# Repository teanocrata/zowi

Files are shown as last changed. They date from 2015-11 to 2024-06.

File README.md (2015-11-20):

# zowi

##License



All these products are released under [Creative Commons Attribution-ShareAlike 4.0 International License](http://creativecommons.org/licenses/by-sa/4.0/).

Todos estos productos están liberados mediante [Creative Commons Attribution-ShareAlike 4.0 International License](http://creativecommons.org/licenses/by-sa/4.0/).

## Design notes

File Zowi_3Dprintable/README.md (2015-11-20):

<table>
<tr>
<td>
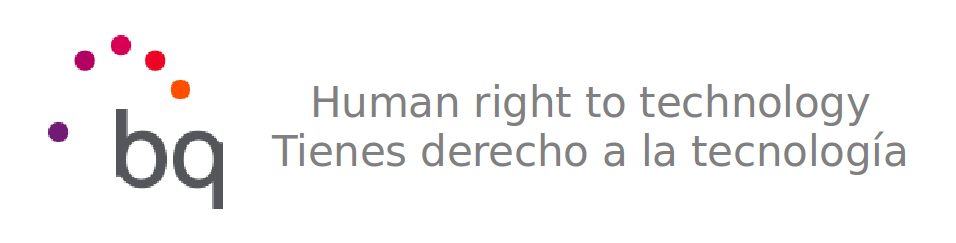
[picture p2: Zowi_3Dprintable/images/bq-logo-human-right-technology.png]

</td>
</tr>
</table>

# ZOWI

In this repository you will find the source files for the **bq Zowi** robot. If you are missing something, please do not hesitate to [file an issue on github](https://github.com/bq/zowiissues)

En este repositorio se encuentran los ficheros fuente del robot **Zowi de bq**. Si echas en falta algo, no dudes en [rellenar una tarea en github](https://github.com/bq/zowi/issues)

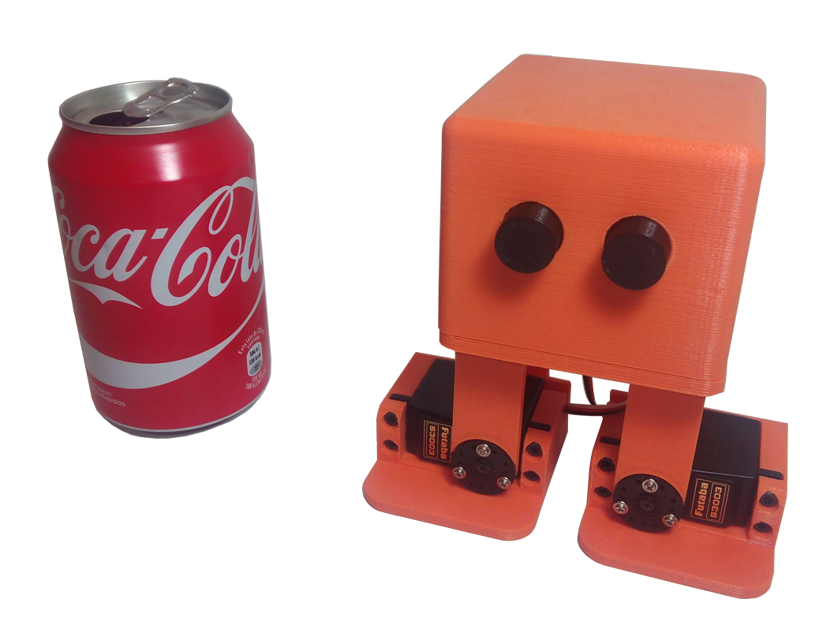
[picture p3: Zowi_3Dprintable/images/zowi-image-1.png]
 

More information in this post in DIWO: [Zowi, introducción a los robots bípedos](http://diwo.bq.com/zowi-introduccion-a-los-robots-bipedos/) (In spanish)

## Designed in Freecad

Zowi is not only an open source robot, but it has also been designed using the open source tool FreeCAD. This way, anyone can open the parts, study them, modify them and distribute the modifications

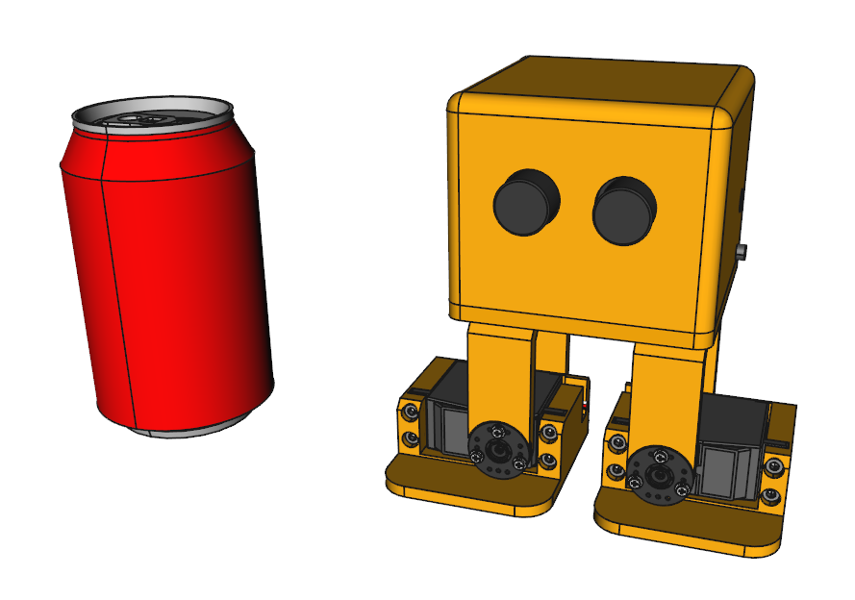
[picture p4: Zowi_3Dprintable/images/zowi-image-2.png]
 

# BOM: Bill of Materials

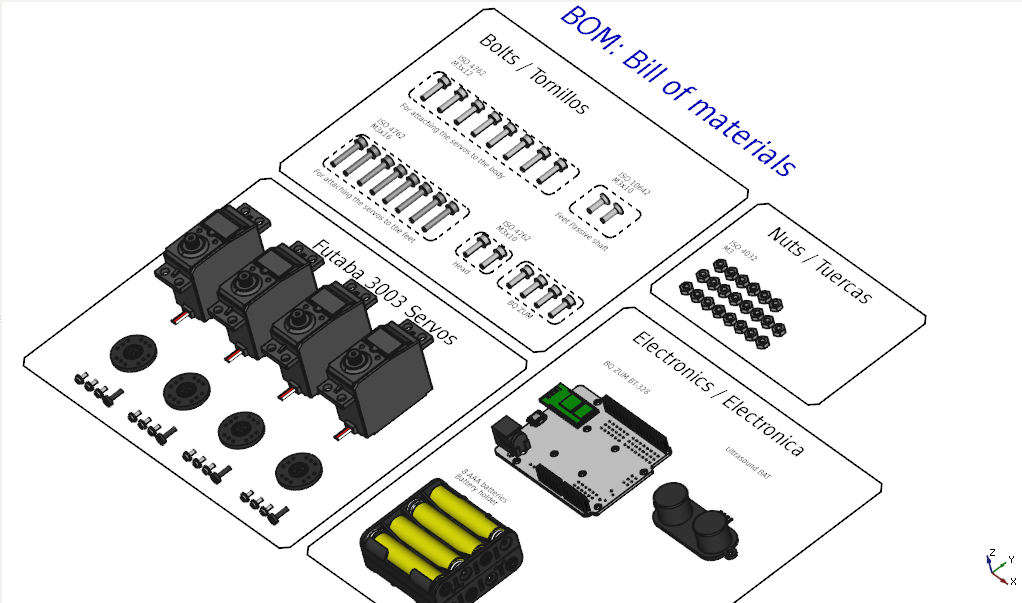
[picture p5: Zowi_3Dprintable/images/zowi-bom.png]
 

* 4 Futaba 3003 servos or compatibles
* 6 M3x10 Bolts (ISO 4762)
* 2 M3x10 Bolts (ISO 10642)
* 8 M3x12 Bolts (ISO 4762)
* 8 M3x16 Bolts (ISO 4762)
* 22 M3 nuts (ISO 4032)
* 1 BQ ZUM BT328 or Arduino
* 4 x 2 AAA Battery holder
* 8 AAA bateries

# License 



This robot is licensed under a [Creative Commons Attribution-ShareAlike 4.0 International License](http://creativecommons.org/licenses/by-sa/4.0/). Please read the LICENSE files for more details.

Este robot tiene una licencia [Creative Commons Attribution-ShareAlike 4.0 International License](http://creativecommons.org/licenses/by-sa/4.0/). Por favor, lea los ficheros LICENSE para más detalles

Original concept by [k120189](http://www.thingiverse.com/k120189/about) on [Thingiverse](http://www.thingiverse.com/thing:43708)

More information: [Zowi CC-BY-SA](http://diwo.bq.com/zowi-cc-by-sa/)

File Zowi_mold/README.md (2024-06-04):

<table>
<tr>
<td>

</td>
</tr>
</table>

# ZOWI

In this repository you will find the source files for the **Zowi** robot. If you are missing something, please do not hesitate to [file an issue on github](https://github.com/bq/zowiissues)

En este repositorio se encuentran los ficheros fuente del robot **Zowi**. Si echas en falta algo, no dudes en [rellenar una tarea en github](https://github.com/bq/zowi/issues)

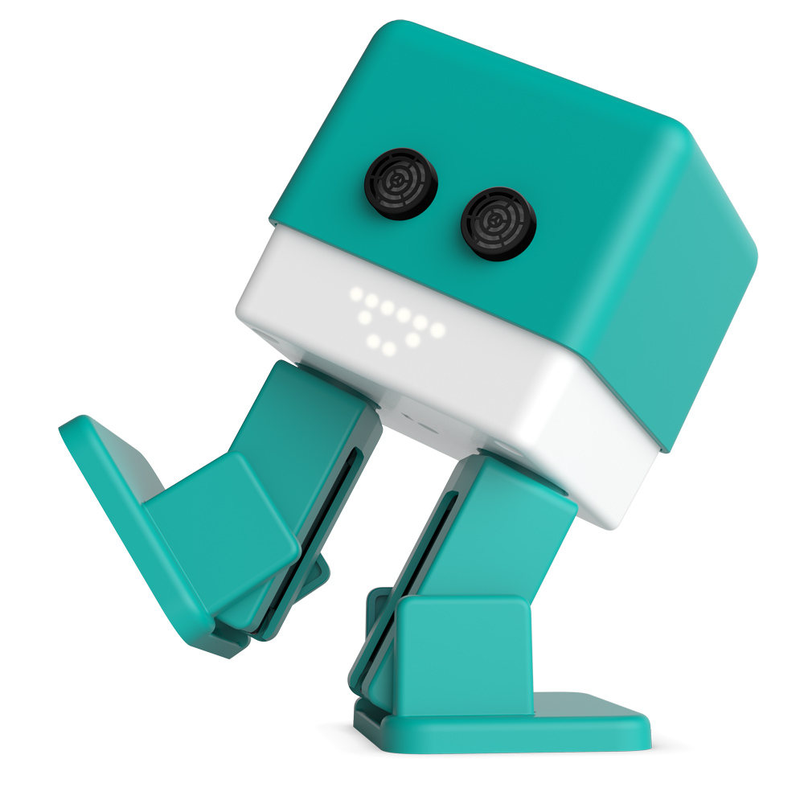
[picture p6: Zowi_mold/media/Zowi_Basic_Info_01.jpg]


More information in the official website: [Zowi](http://zowi.bq.com/)

# License



This robot is licensed under a [Creative Commons Attribution-ShareAlike 4.0 International License](http://creativecommons.org/licenses/by-sa/4.0/). Please read the LICENSE files for more details.

Este robot tiene una licencia [Creative Commons Attribution-ShareAlike 4.0 International License](http://creativecommons.org/licenses/by-sa/4.0/). Por favor, lea los ficheros LICENSE para más detalles

Derived from [Zowi by bqlabs](https://github.com/bqlabs/zowi)

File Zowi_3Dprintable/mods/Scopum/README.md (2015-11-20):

# Scopum

Scopum has been created by [HackLab UPM Bq](http://hacklabupm.bq.com/doku.php?id=start). 
He has been designed in order to have a battle with more Scopums. He has a target in the chest with a receptor fototransistor and a emisor diode in the weapon which is in his arm. Besides, he include a buzzer destinated to make sound when he shoots and when he dies.

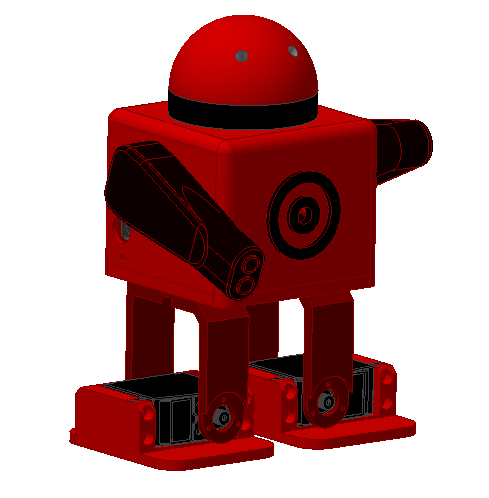
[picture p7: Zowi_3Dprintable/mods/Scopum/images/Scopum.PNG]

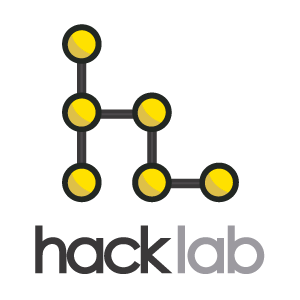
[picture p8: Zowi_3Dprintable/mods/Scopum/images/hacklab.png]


Original concept by [JavierIH](https://github.com/JavierIH) on [Github](https://github.com/bq/zowi)

# License 



This robot is licensed under a [Creative Commons Attribution-ShareAlike 4.0 International License](http://creativecommons.org/licenses/by-sa/4.0/). Please read the LICENSE files for more details.

Este robot tiene la licencia [Creative Commons Attribution-ShareAlike 4.0 International License](http://creativecommons.org/licenses/by-sa/4.0/). Por favor, lea los ficheros LICENSE para más detalles

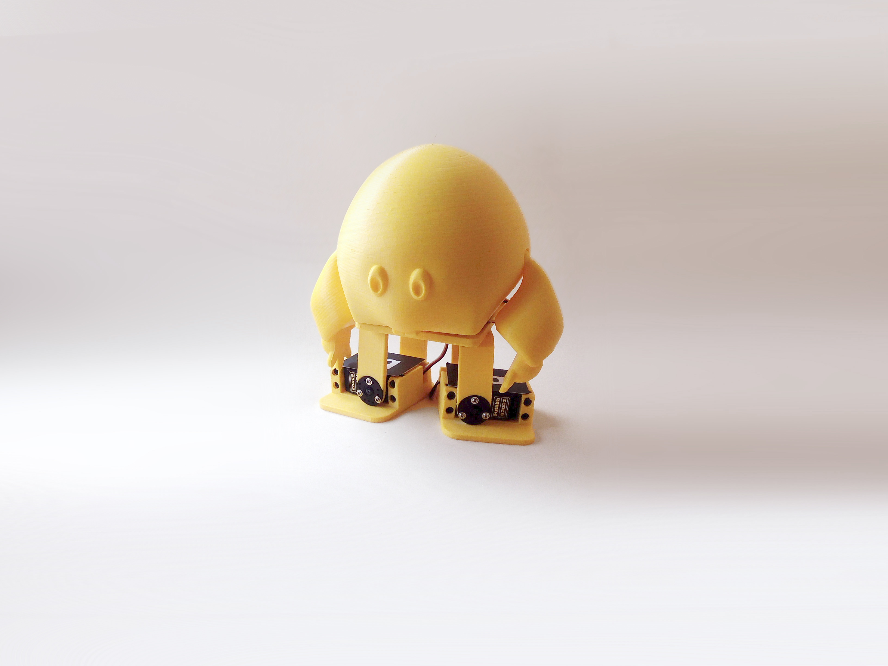
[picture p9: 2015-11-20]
Zowi_3Dprintable/mods/JIM/images/JIM_2.jpg

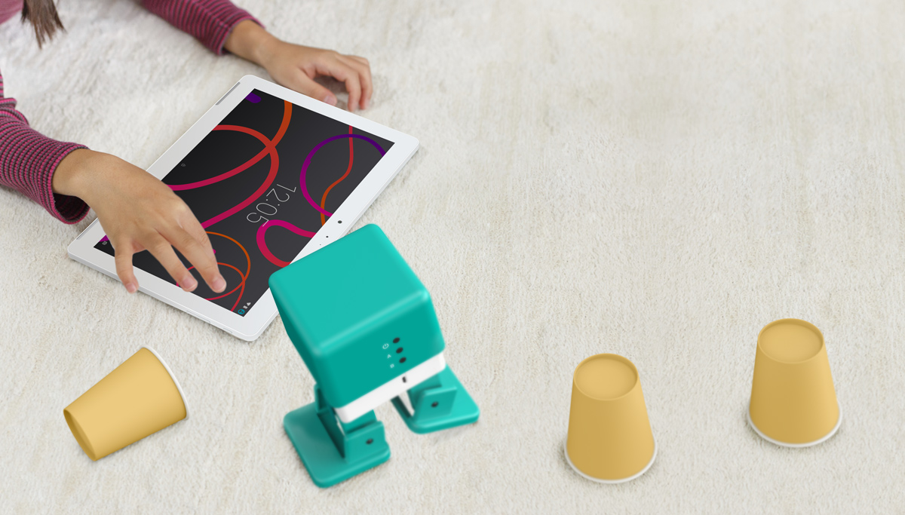
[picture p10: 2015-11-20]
Zowi_mold/media/Zowi_Integracion_app_dise2.jpg

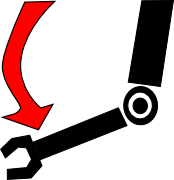
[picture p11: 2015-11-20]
Zowi_3Dprintable/mods/Scopum/code/Protocoder/images/izquierdo_abajo.png

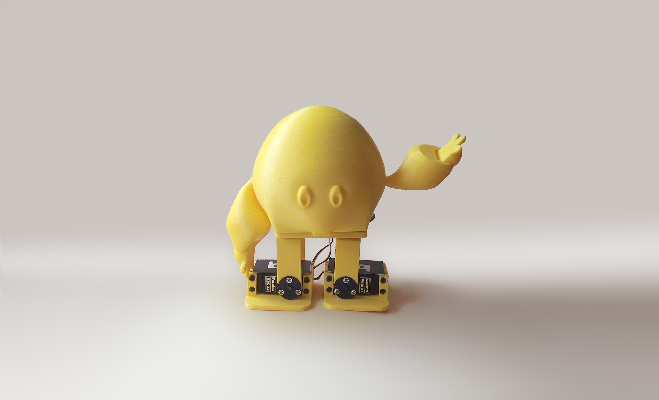
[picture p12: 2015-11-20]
Zowi_3Dprintable/mods/JIM/images/JIM_1.jpg

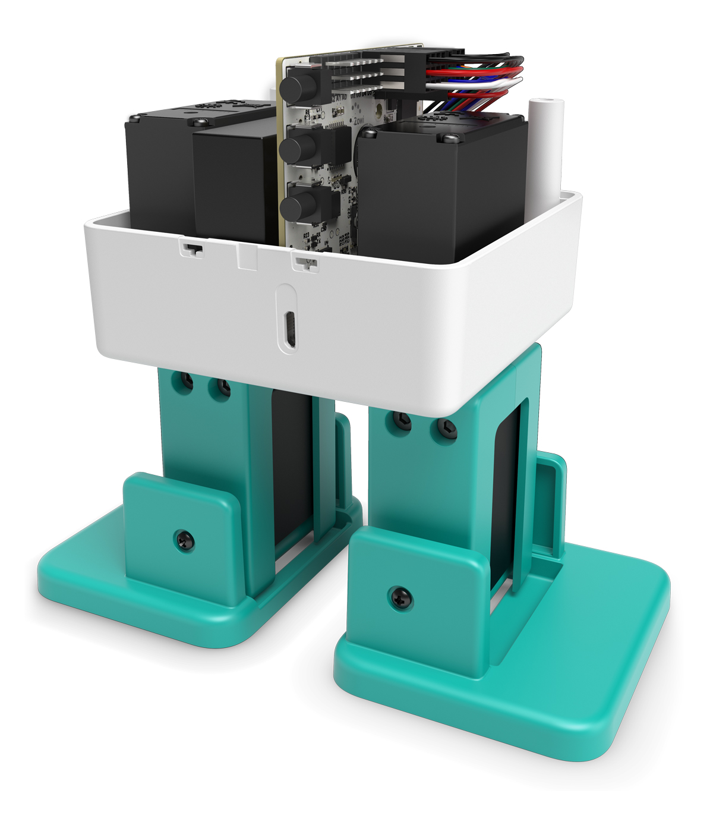
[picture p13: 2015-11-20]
Zowi_mold/media/Zowi_lookbook_interior_01.jpg

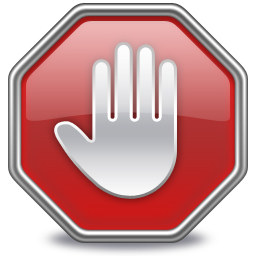
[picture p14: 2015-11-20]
Zowi_3Dprintable/code/protocoder/images/stop.png

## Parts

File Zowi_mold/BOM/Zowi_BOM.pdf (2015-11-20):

Name | Quantity | Made in
Electronics | Main Board | 1 | Valencia (Spain)
| LED Matrix | 1 | Valencia (Spain)
| Ultrasonic Board | 1 | Valencia (Spain)
| Battery 4040mAh | 1 | Valencia (Spain)
| Futaba S3003 servo | 4 | Taiwan
| Ultrasonic cable | 1 | China
| LED Matrix cable | 1 | China
| MJ622 black round button | 3 | France
| Light filter | 1 | Madrid (Spain)
Plastic parts | Zowi Top housing | 1 | Poland
| Zowi Base | 1 | Poland
| Zowi Leg back | 2 | Poland
| Zowi Leg front | 2 | Poland
| Zowi Foot left | 1 | Poland
| Zowi Foot right | 1 | Poland
| Zowi Foot cover | 2 | Poland
Screws | Socket head cap screws M3x10 (DIN912) Black | 20 | Navarra (spain)
| Celoplast screws for plastic CL 81 Z - Ø2.3 x 6mm Zin | 2 | Spain/China
| Celoplast screws for plastic CL 81 Z - Ø2.0 x 8mm Zin | 6 | Spain/China
| TH030H055 inserts for M3 screws | 20 | France

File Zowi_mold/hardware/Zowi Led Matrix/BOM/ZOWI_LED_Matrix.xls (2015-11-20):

 |  |  |  |  | BILL OF MATERIALS
TITLE: | BOM-Complete For Project [ZOWI_LED_Matrix.PrjPcb] (No PCB Document Selected) |  | REV | DATE | AUTHOR |  | DATE | AUTHOR
VARIANT: |  |  | 00 | 16/11/2015 | Jon Goitia | MADE BY: | 16/11/2015 | Jon Goitia
DOCUMENT: | Bill of Materials |  | 01 |  |  | VERIFIED BY:
PROJECT: | ZOWI_LED_Matrix.PrjPcb |  | 02 |  |  | APPROVED BY:
NOTE | ITEM | Designator | Description |  |  | OrderingCode | Manufacturer | Footprint | Quantity | Value
 | 1 | C1, C6 | Capacitor SMD |  |  | C0603C225K4PAC | Kemet | C0603 | 2 | 2.2uF ±10% 16V
 | 2 | C2, C3, C4, C5 | Capacitor SMD |  |  | C0402C104K4RAC | Kemet | C0402 | 4 | 100nF ±10% 16V
 | 3 | D1, D2, D3, D4 | Protection, Transient Suppression Diode |  |  | ESD9L5.0ST5G | ON Semiconductor | SOD923 | 4
 | 4 | J1 | Connector, 1x5 MTE Angled Header 2.54mm |  |  | 5-103635-4 | TE Connectivity | 1x5 MTE Angled Header 2.54mm | 1 | 5
 | 5 | LD1A, LD1B, LD1C, LD1D, LD1E, LD1F, LD2A, LD2B, LD2C, LD2D, LD2E, LD2F, LD3A, LD3B, LD3C, LD3D, LD3E, LD3F, LD4A, LD4B, LD4C, LD4D, LD4E, LD4F, LD5A, LD5B, LD5C, LD5D, LD5E, LD5F | LED |  |  | LTW-170ZDC | Lite-On | LED0805 | 30 | White
 | 6 | R1, R2, R3, R4, R5, R6, R7, R8 | Resistor |  |  | CAY16-271J4LF | Bourns | 4xArray_1206 | 8 | 270R ±0,5% 0,0625W
 | 7 | U1, U2, U3, U4 | Shift Register 8BIT |  |  | 74HC595BQ | NXP | DHVQFN16-2.5x3.5MM | 4
NOTES:

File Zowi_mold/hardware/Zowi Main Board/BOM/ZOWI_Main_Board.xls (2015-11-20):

 |  |  |  |  | BILL OF MATERIALS
TITLE: | BOM_Complete For Project [ZOWI_Main_Board.PrjPCB] (No PCB Document Selected) |  | REV | DATE | AUTHOR |  | DATE | AUTHOR
VARIANT: |  |  | 00 | 26/10/2015 | Raúl de Pablos | MADE BY: | 26/10/2015 | Raúl de Pablos
DOCUMENT: | Bill of Materials |  | 01 |  |  | VERIFIED BY:
PROJECT: | ZOWI_Main_Board.PrjPCB |  | 02 |  |  | APPROVED BY:
NOTE | ITEM | Designator | Description |  |  | OrderingCode | Manufacturer | Footprint | Quantity | OrderingCode 2 | Manufacturer 2 | Value
 | 1 | BUZZ2 | Buzzer |  |  | KXG1205 | Kingstate Elect. | BUZZER_12 | 1
 | 2 | C1, C2, C8, C11, C12, C13, C14, C17, C23, C26, C27, C30, C31, C33, C36, C50, C52 | Capacitor SMD |  |  | C0402C104K4RAC | Kemet | C0402 | 17 |  |  | 100nF ±10% 16V
 | 3 | C3, C4, C5, C24, C25, C28, C35, C49 | Capacitor SMD |  |  | C0603C105K4PAC | Kemet | C0603 | 8 |  |  | 1uF ±10% 16V
 | 4 | C9 | Capacitor SMD |  |  | GJM1555C1H120JB01D | Murata | C0402 | 1 |  |  | 12pF ±5% 50V
 | 5 | C10 | Capacitor SMD |  |  | C1608X5R1C475K080AC | TDK | C0603 | 1 |  |  | 4.7uF ±10% 16V
 | 6 | C15, C40, C45 | Capacitor SMD |  |  | C0603C225K4PAC | Kemet | C0603 | 3 |  |  | 2.2uF ±10% 16V
 | 7 | C16, C18, C19, C20, C21 | Capacitor SMD |  |  | GRM219R61C226ME15K | Murata | C0805 | 5 |  |  | 22uF ±20% 16V
 | 8 | C22 | Capacitor, Electrolytic, SMD |  |  | EEE-0JA221WP | Panasonic | CASE_D | 1 |  |  | 220uF 6V3
 | 9 | C32, C39, C44, C47, C51 | Capacitor SMD |  |  | C0402C103K4RAC | Kemet | C0402 | 5 |  |  | 10nF ±10% 16V
 | 10 | C34 | Capacitor SMD |  |  | C2012X7R2E472K085AM | TDK | C0805 | 1 |  |  | 4700pF ±10% 250V
 | 11 | C37, C38 | Capacitor SMD |  |  | C0402C470K4GAC | Kemet | C0402 | 2 |  |  | 47pF ±10% 16V
 | 12 | C41, C42 | Capacitor SMD |  |  | C0402C100K4GAC | Kemet | C0402 | 2 |  |  | 10pF ±10% 16V
 | 13 | C43 | Capacitor SMD |  |  | GRM1555C1H180JA01D | Murata | C0402 | 1 |  |  | 18pF ±5% 50V
 | 14 | C46 | Capacitor SMD |  |  | C0402C150K4GAC | Kemet | C0402 | 1 |  |  | 15pF ±10% 16V
 | 15 | C48 | Capacitor SMD |  |  | C0402C473K4RAC | Kemet | C0402 | 1 |  |  | 47nF ±10% 16V
 | 16 | Cs1 | Capacitor SMD |  |  | GJM1555C1H3R7WB01D | Murata | C0402 | 1 |  |  | 3,7pF ±7% 50V
 | 17 | D1, D4 | Dual Schottky Diode |  |  | BAT54S | NXP | SOT23-3 | 2 | BAT54S | Vishay | 200mA 30V
 | 18 | D2, D3 | Schottky Diode |  |  | PMEG3030EP | NXP | SOD128 | 2 |  |  | 3A 30V
 | 19 | F1 | Protection, PTC Resettable Fuse |  |  | MF-MSMF150/24X | Bourns | F1812 | 1
 | 20 | F2 | Protection, USB ESD |  |  | 82400152 | Würth | SOT563 | 1 | CDSOT563-0502 | Bourns
 | 21 | F3 | Filter, Band Pass, Balun |  |  | 2450FB15K0005E | Johanson Technlogy | 2450FB15K0005 | 1 | DBF81F104-CSR-T | Soshin
 | 22 | J1 | Connector, 1x6 pin Header 2.54mm |  |  | TSW-106-07-T-S-BLUE | Samtec | 1x6 Pin Header 2.54 | 1
 | 23 | J2 | Connector, 1x6 pin Header 2.54mm |  |  | TSW-106-07-T-S-RED | Samtec | 1x6 Pin Header 2.54 | 1
 | 24 | J3 | Connector, 1x6 pin Header 2.54mm |  |  | TSW-106-07-T-S | Samtec | 1x6 Pin Header 2.54 | 1 | 613 006 111 21 | Würth Elektronik | 6
 | 25 | J4 | Connector, 6 pin Dual Header 2.54mm |  |  | TSW-103-07-T-D | Samtec | 2x3 Pin Header 2.54 | 1 | 613 006 211 21 | Würth Elektronik | 6
 | 26 | J5, J8 | Connector, 1x4 pin Header 2.54mm |  |  | TSW-104-07-T-S | Samtec | 1x4 Pin Header 2.54 | 2 | 613 004 111 21 | Würth Elektronik | 4
 | 27 | J6 | Connector, 1x4 pin Header 2.54mm |  |  | TSW-104-07-T-S-NATURAL | Samtec | 1x4 Pin Header 2.54 | 1
 | 28 | J7 | Connector, 1x4 pin Header 2.54mm |  |  | TSW-104-07-T-S-RED | Samtec | 1x4 Pin Header 2.54 | 1
 | 29 | J9 | 1x3 PH connector |  |  | S3B-PH-SM4-TB | JST | S3B-PH-SM4-TB | 1
 | 30 | J10 | Connector, USB Micro B |  |  | 10118194-0001LF | FCI | USB_B_W_REAR_PEGS | 1
 | 31 | L1 | Inductor, Power, SMD |  |  | SRN5040-1R5Y | Bourns | SRN5040 | 1 |  |  | 1.5uH 3,5A
 | 32 | L2 | Ferrite Bead |  |  | BLM18SG121TN1D | Murata | L0603 | 1 |  |  | 120R 0,025R 3000mA
 | 33 | L3 | Inductor SMD |  |  | LQG15HS15NJ02D | Murata | L0402 | 1 |  |  | 15nH 0,3A
 | 34 | LD1 | LED |  |  | APA3010SURCK | KingBright | LED_SMD_RA | 1 |  |  | Red
 | 35 | LD3 | LED |  |  | LTST-C194TBKT | Lite-On | LED0603 | 1 | HSMN-C120 | Avago Technologies | Blue
 | 36 | Q1 | NFET |  |  | FDV301N | Fairchild Semiconductor | SOT23-3 | 1
 | 37 | R1, R5, R22, R36 | Resistor, SMD, Resistor, SMD, Resistor, SMD, Resistor |  |  | CRCW04021M00JNED | Vishay | R0402 | 4 |  |  | 1M ±5% 0.063W
 | 38 | R2, R29, R30 | Resistor, SMD |  |  | CRCW0402220RJN | Vishay | R0402 | 3 |  |  | 220R ±5% 0.063W
 | 39 | R3 | Resistor, SMD |  |  | CRCW040251K0JN | Vishay | R0402 | 1 |  |  | 51k ±5% 0.063W
 | 40 | R4, R6, R7, R9, R12, R13, R14, R15, R31, R34, R35 | Resistor, SMD |  |  | CRCW040210K0JN | Vishay | R0402 | 11 |  |  | 10k ±5% 0.063W
 | 41 | R10, R11, R21 | Resistor, SMD |  |  | CRCW0402130KFK | Vishay | R0402 | 3 |  |  | 130k ±1% 0.063W
 | 42 | R17 | Resistor, SMD |  |  | CRCW0402470RJN | Vishay | R0402 | 1 |  |  | 470R ±5% 0.063W
 | 43 | R18 | Resistor, SMD |  |  | CRCW0402560RFK | Vishay | R0402 | 1 |  |  | 560R ±1% 0.063W
 | 44 | R20 | Resistor, SMD |  |  | CRCW0402680KFK | Vishay | R0402 | 1 |  |  | 680k ±1% 0.063W
 | 45 | R23, R24, R26, R28 | Resistor, SMD |  |  | CRCW04021K00JN | Vishay | R0402 | 4 |  |  | 1k ±5% 0.063W
 | 46 | R25 | Resistor, SMD |  |  | CRCW06031M00JN | Vishay | R0603 | 1 |  |  | 1M ±5% 0.1W
 | 47 | R27 | Resistor, SMD |  |  | CRCW04022R20JN | Vishay | R0402 | 1 |  |  | 2R2 ±5% 0.063W
 | 48 | R32 | Resistor, SMD |  |  | CRCW0402270RJN | Vishay | R0402 | 1 |  |  | 270R ±5% 0.063W
 | 49 | R33 | Resistor, SMD |  |  | CRCW0402150KJN | Vishay | R0402 | 1 |  |  | 150k ±5% 0.063W
 | 50 | R37 | Resistor, SMD |  |  | CRCW040216K0JN | Vishay | R0402 | 1 |  |  | 16k ±5% 0.063W
 | 51 | R38 | Resistor, SMD |  |  | CRCW040230K0JN | Vishay | R0402 | 1 |  |  | 30k ±5% 0.063W
 | 52 | RX1, TX1 | LED |  |  | HSMG-C190 | Avago Technologies | LED0603 | 2 | LG Q971-KN-1 | OSRAM Opto | Green
 | 53 | SW1, SW2, SW3 | Micro miniature pushbutton surface Switch |  |  | MJTP1105T | APEM | MJTP1105T | 3
 | 54 | U1 | Processor, 8-bit AVR Microcontroller |  |  | ATMEGA328P-AU | Atmel | TQFP32 | 1
 | 55 | U2 | Microphone MEMS audio surface-mount |  |  | MP33AB01HTR | ST Microelectronics | RHLGA | 1
 | 56 | U3 | Operational Amplifier Dual |  |  | LM358PT | ST | TSSOP8 | 1 | LM358PWR | Texas Instruments
 | 57 | U4 | EEPROM Memory I2C 1KBIT 400KHZ SOT23-5 |  |  | 24AA01T-I/OT | Microchip | SOT23-5 | 1
 | 58 | U5 | Battery Charger, Li-Po/Li-ion, Single Cell |  |  | BQ24090DGQR | Texas Instruments | MSOP-10_5x3MM | 1
 | 59 | U6 | Synchronous Boost Regulator with Bi-Directional Load Disconnect |  |  | MP3421GG-Z | MPS | QFN14_2X2 | 1
 | 60 | U7 | LDO 300mA |  |  | MIC5504-3.3YM5 TR | Micrel | SOT23-5 | 1
 | 61 | U8 | Smart push-button on/off controller |  |  | STM6601CQ2BDM6F | ST Microelectronics | TDFN12 | 1
 | 62 | U9 | USB to UART Transceiver |  |  | CP2104-F03-GMR | Silicon Labs | QFN24 | 1
 | 63 | U10 | Bluetooth Modem, 2.4-GHz Bluetooth SoC |  |  | BC417143B-GIQN-E4 | CSR | TFBGA96P8X8 | 1
 | 64 | U11 | Memory NOR Flash 8-Mbit 3 V supply |  |  | S29AL008J70BFI02 | Spansion | TFBGA48P6X8 | 1 | M29W800DB70ZE6E | Micron | 8MB
 | 65 | U12 | Multiplexer/demultiplexer Quad |  |  | SN74CBT3257CPWR | Texas Instruments | TSSOP16 | 1
 | 66 | Y1 | Resonator 3 pin |  |  | CSTCE16M0V53-R0 | Murata | Resonator_1.3x3.2 | 1 |  |  | 16MHz
 | 67 | Y2 | Crystal 4 pin |  |  | ABM8-26.000MHZ-10-1-U-T | Abracon | XTAL 3.2x2.5 | 1 | 403C11A26M00000 | CTS | 26MHz
NOTES:

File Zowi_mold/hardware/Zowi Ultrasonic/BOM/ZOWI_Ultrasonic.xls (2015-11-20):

 |  |  |  |  | BILL OF MATERIALS
TITLE: | BOM_Complete For Variant [Zowi] of Project [ZOWI_Ultrasonic.PrjPcb] (No PCB Document Selected) |  | REV | DATE | AUTHOR |  | DATE | AUTHOR
VARIANT: |  |  | 00 | 16/11/2015 | Álvaro Hernando | MADE BY: | 16/11/2015 | Álvaro Hernando
DOCUMENT: | Bill of Materials |  | 01 |  |  | VERIFIED BY:
PROJECT: | ZOWI_Ultrasonic.PrjPcb |  | 02 |  |  | APPROVED BY:
NOTE | ITEM | Designator | Description |  |  | OrderingCode | Manufacturer | Footprint | Quantity | Value
 | 1 | C1, C2, C9, C14 | Capacitor SMD |  |  | C0402C104K4RAC | Kemet | C0402 | 4 | 100nF ±10% 16V
 | 2 | C3, C4, C5, C6, C7, C15 | Capacitor SMD |  |  | C0603C105K4PAC | Kemet | C0603 | 6 | 1uF ±10% 16V
 | 3 | C8, C10, C13 | Capacitor SMD |  |  | C0402C103K4RAC | Kemet | C0402 | 3 | 10nF ±10% 16V
 | 4 | C11, C12 | Capacitor SMD |  |  | C0402C102K4RAC | Kemet | C0402 | 2 | 1nF ±10% 16V
 | 5 | C16 | Capacitor SMD |  |  | EMK107BBJ106MA-T | Taiyo Yuden | C0603 | 1 | 10uF ±20% 16V
 | 6 | D1 | Protection, Bidirectional Transient Suppression Diodes |  |  | ESD9B5.0ST5G | ON Semiconductor | SOD923 | 1
 | 7 | D2, D3 | Protection, Transient Suppression Diode |  |  | ESD9L5.0ST5G | ON Semiconductor | SOD923 | 2
 | 8 | J1 | Connector, 1x4 MTE Angled Header 2.54mm |  |  | 5-103635-3 | TE Connectivity | 1x4 MTE Angled Header 2.54mm | 1 | 4
 | 9 | Q1, Q2 | PFET |  |  | BSS84 | Fairchild Semiconductor | SOT23-3 | 2
 | 10 | Q3 | NFET |  |  | FDV301N | Fairchild Semiconductor | SOT23-3 | 1
 | 11 | R1, R4, R5, R6, R7, R11, R15, R18, R24 | Resistor, SMD |  |  | CRCW040210K0JN | Vishay | R0402 | 9 | 10k ±5% 0.063W
 | 12 | R3, R8, R20 | Resistor, SMD |  |  | CRCW04021K00JN | Vishay | R0402 | 3 | 1k ±5% 0.063W
 | 13 | R9 | Resistor, SMD |  |  | CRCW040275K0JN | Vishay | R0402 | 1 | 75k ±5% 0.063W
 | 14 | R10, R13 | Resistor, SMD |  |  | CRCW0402120KJN | Vishay | R0402 | 2 | 120k ±5% 0.063W
 | 15 | R12 | Resistor, SMD |  |  | CRCW06031M00JN | Vishay | R0603 | 1 | 1M ±5% 0.1W
 | 16 | R14, R17, R21 | Resistor, SMD |  |  | CRCW04023K90JN | Vishay | R0402 | 3 | 3k9 ±5% 0.063W
 | 17 | R16, R22 | Resistor, SMD |  |  | CRCW040256K0JN | Vishay | R0402 | 2 | 56k ±5% 0.063W
 | 18 | R19 | Resistor, SMD |  |  | CRCW040220K0JN | Vishay | R0402 | 1 | 20k ±5% 0.063W
 | 19 | R23, R25 | Resistor, SMD |  |  | CRCW040210K0FK | Vishay | R0402 | 2 | 10k ±1% 0.063W
 | 20 | R26, R27, R28 | Resistor, SMD |  |  | CRCW0402220RJN | Vishay | R0402 | 3 | 220R ±5% 0.063W
 | 21 | U1 | Processor, 32-bit microcontroller |  |  | MKE04Z8VTG4 | Freescale | TSSOP16 | 1
 | 22 | U2 | Dual RS-232 Driver/Receiver |  |  | MAX232EIPWR | Texas Instruments | TSSOP16 | 1
 | 23 | U3 | Operational Amplifier Quadruple |  |  | LM324PWR | Texas Instruments | TSSOP14 | 1
 | 24 | US1 | Ultrasonic Sensor |  |  | NU40C16T-2 | Jinci | NU40C16 | 1
 | 25 | US2 | Ultrasonic Sensor |  |  | NU40C16R-2 | Jinci | NU40C16 | 1
NOTES:

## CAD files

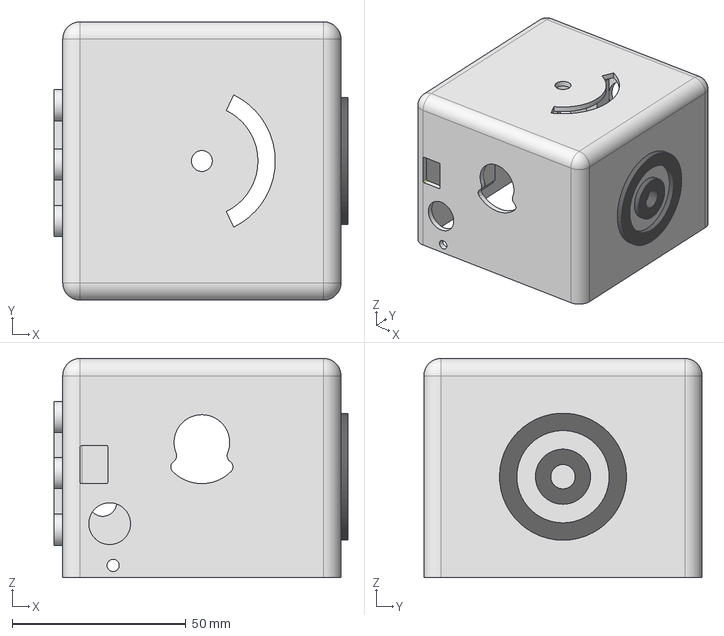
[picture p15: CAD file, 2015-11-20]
Zowi_3Dprintable/mods/Scopum/parts/step/body.step
84.5 x 80.0 x 63.0 mm

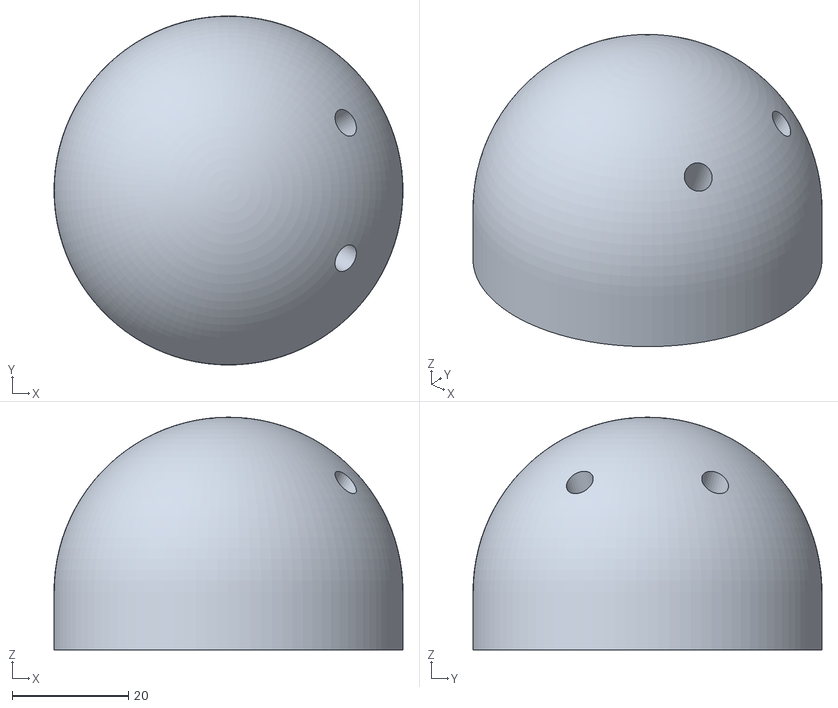
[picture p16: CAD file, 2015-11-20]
Zowi_3Dprintable/mods/Scopum/parts/stl/head.stl
60.0 x 60.0 x 40.0

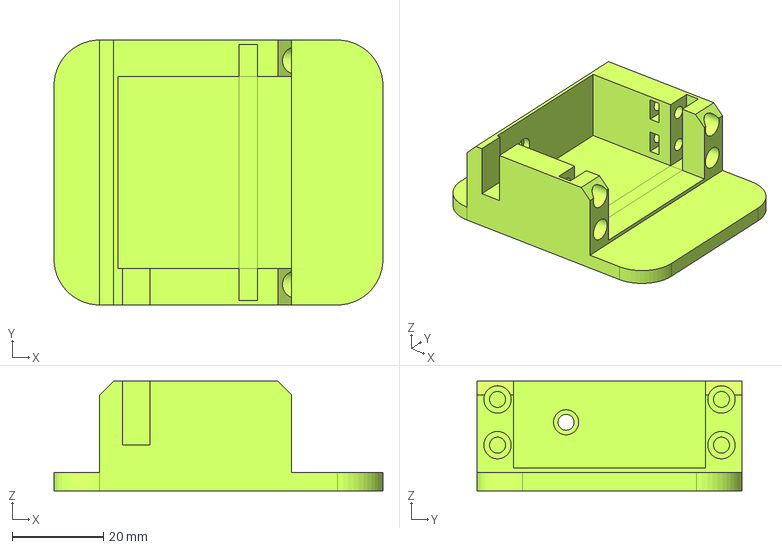
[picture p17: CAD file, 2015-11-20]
Zowi_3Dprintable/parts/step/footL.step
72.0 x 58.0 x 24.0 mm

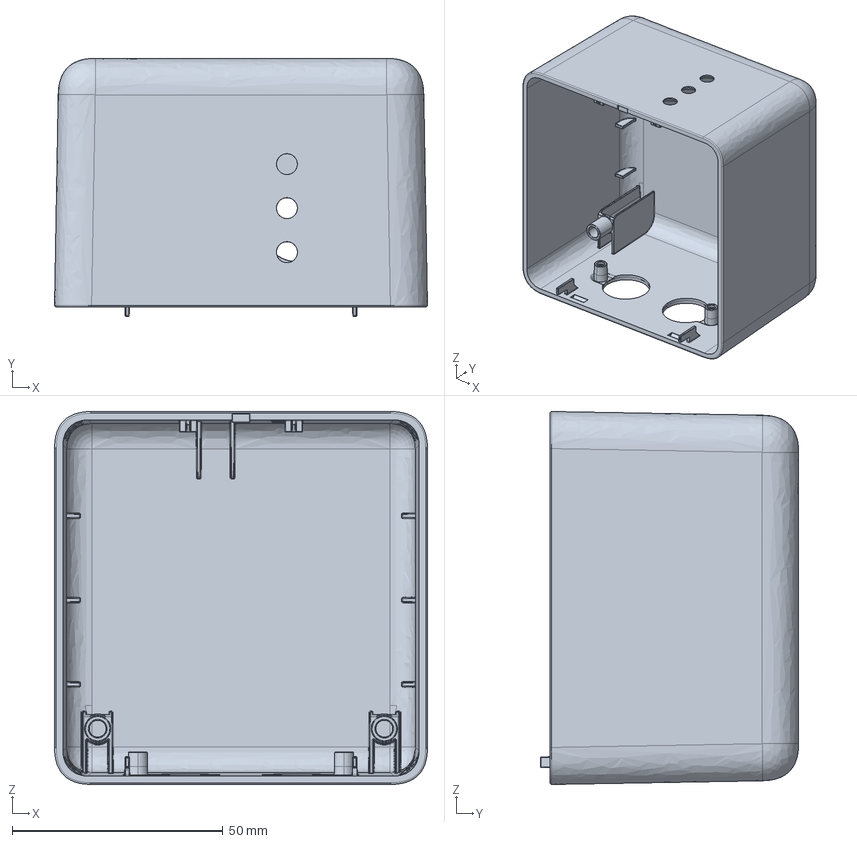
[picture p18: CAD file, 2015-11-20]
Zowi_mold/plastic_parts/STP/Zowi_top_housing.stp
88.5 x 61.3 x 88.5 mm

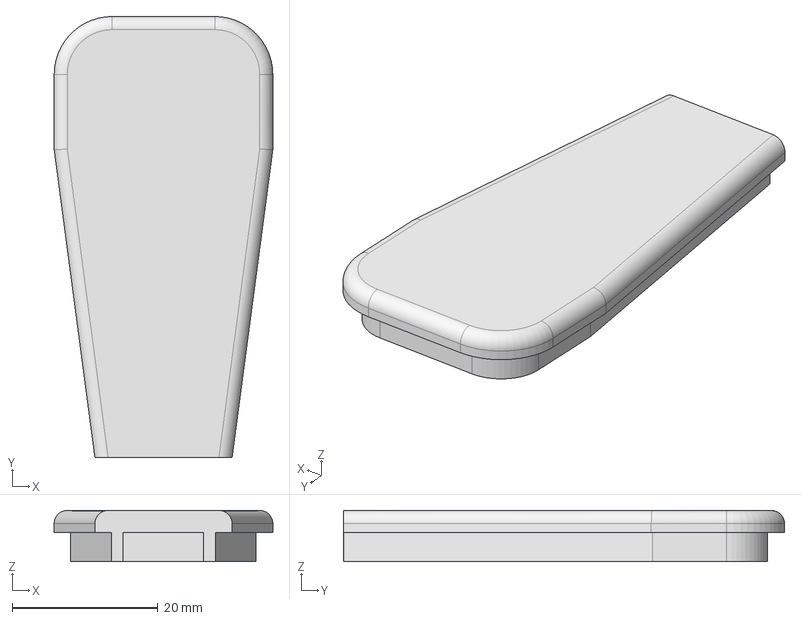
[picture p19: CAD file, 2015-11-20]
Zowi_3Dprintable/mods/Scopum/parts/step/arm_weapon_part2.step
30.0 x 60.5 x 7.00 mm

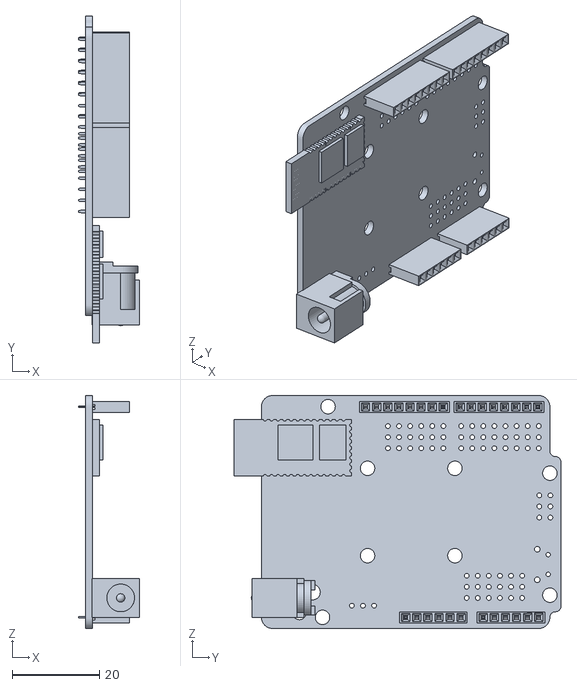
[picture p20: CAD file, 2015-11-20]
Zowi_3Dprintable/mods/Scopum/parts/stl/ZUM_BT_328.stl
14.0 x 74.9 x 53.4

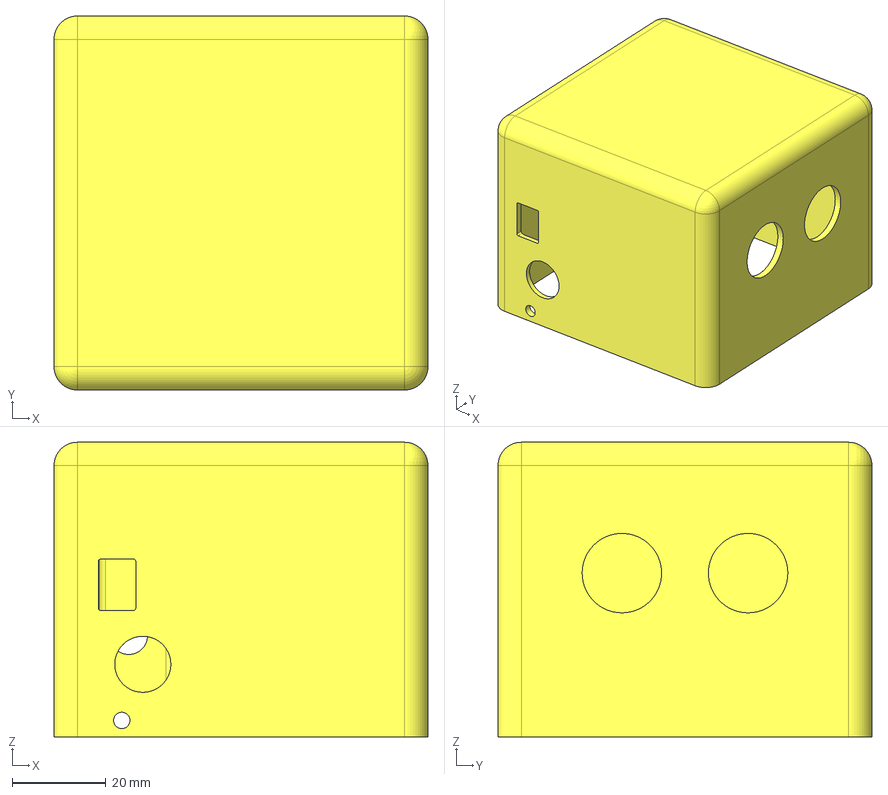
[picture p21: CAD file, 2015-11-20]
Zowi_3Dprintable/parts/step/body.step
80.0 x 80.0 x 63.0 mm

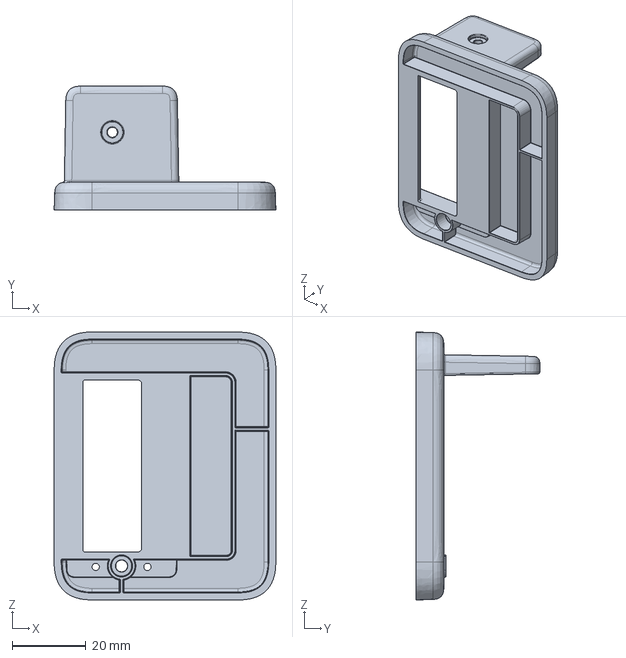
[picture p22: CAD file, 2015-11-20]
Zowi_mold/plastic_parts/STP/Zowi_foot_left.stp
60.0 x 33.5 x 72.5 mm

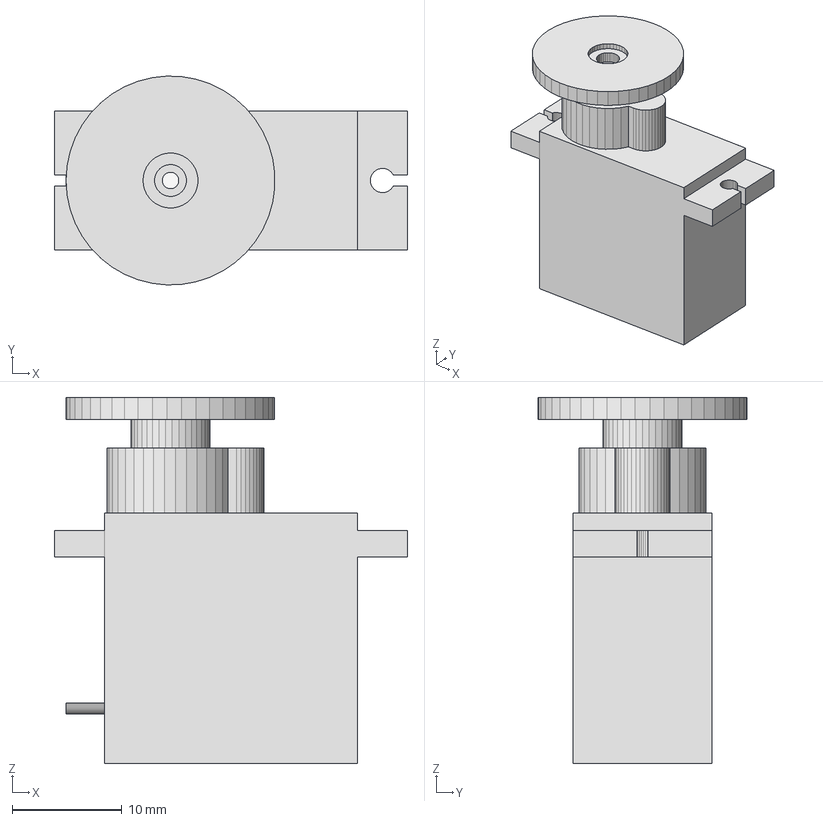
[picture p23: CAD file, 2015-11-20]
Zowi_3Dprintable/mods/Scopum/parts/step/servo_mini.step
32.1 x 19.0 x 33.3 mm

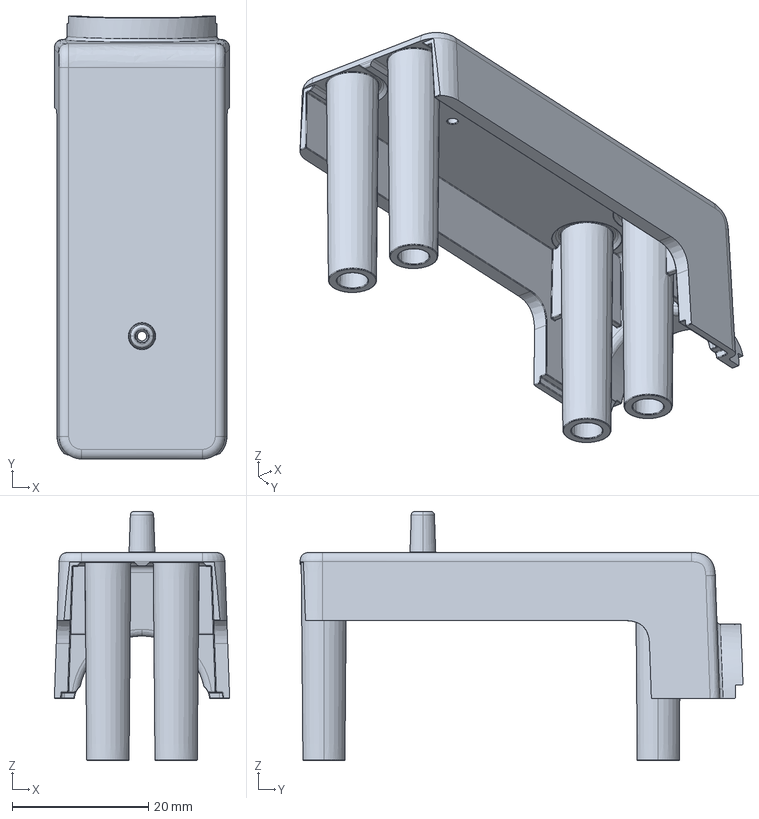
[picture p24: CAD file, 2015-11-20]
Zowi_mold/plastic_parts/STP/Zowi_leg.stp
25.7 x 64.9 x 36.5 mm

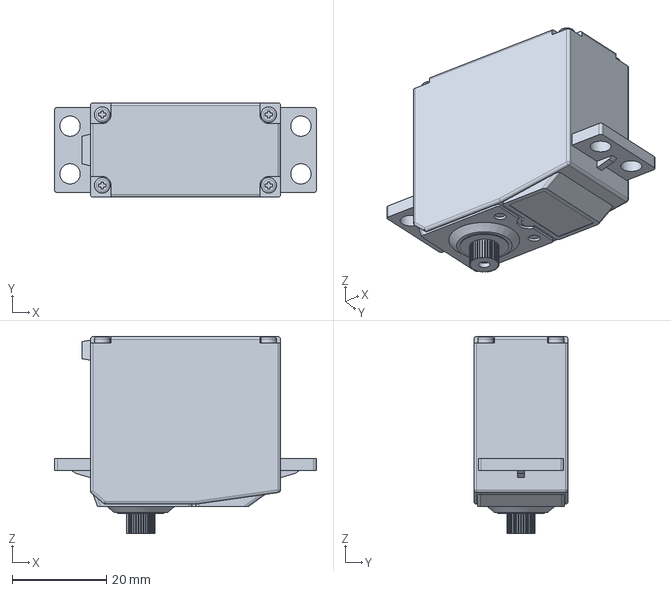
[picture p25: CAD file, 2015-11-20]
Zowi_3Dprintable/mods/Scopum/parts/step/servo.step
55.5 x 20.0 x 41.7 mm

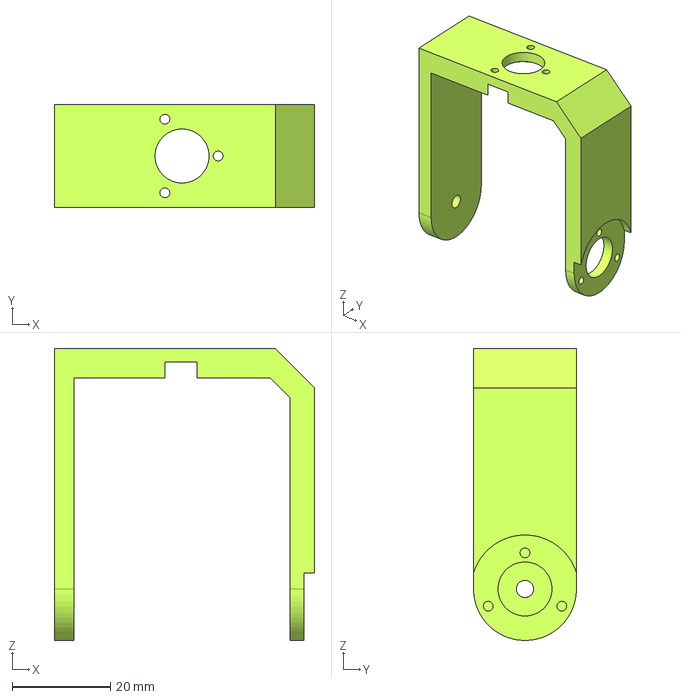
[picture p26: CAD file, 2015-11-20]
Zowi_3Dprintable/parts/step/leg.step
53.0 x 21.0 x 59.5 mm

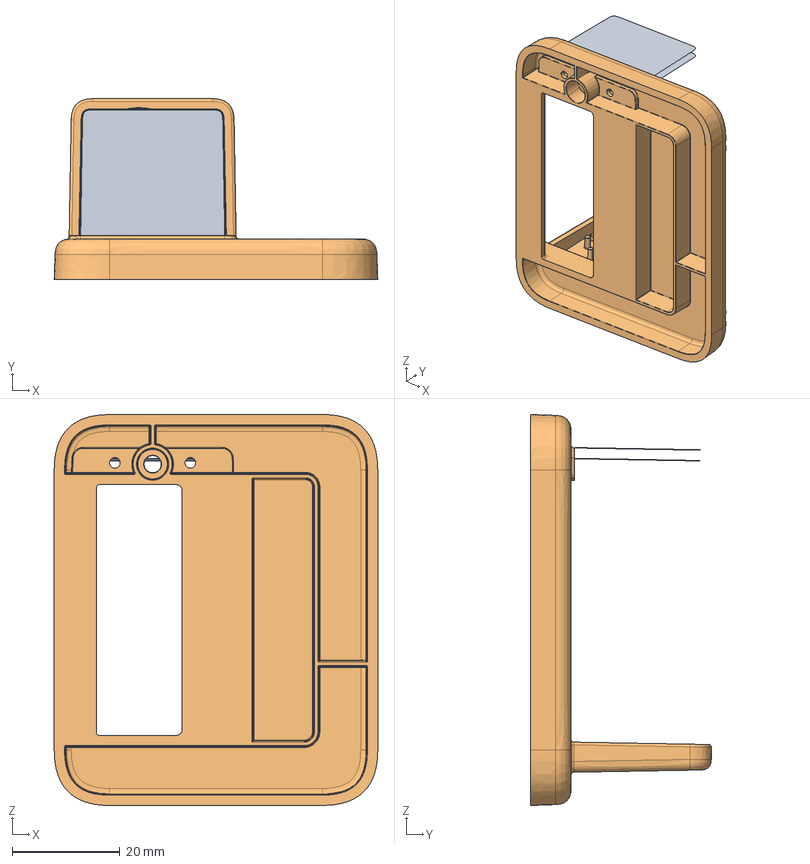
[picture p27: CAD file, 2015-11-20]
Zowi_mold/plastic_parts/STP/Zowi_foot_right.stp
60.0 x 33.5 x 72.5 mm

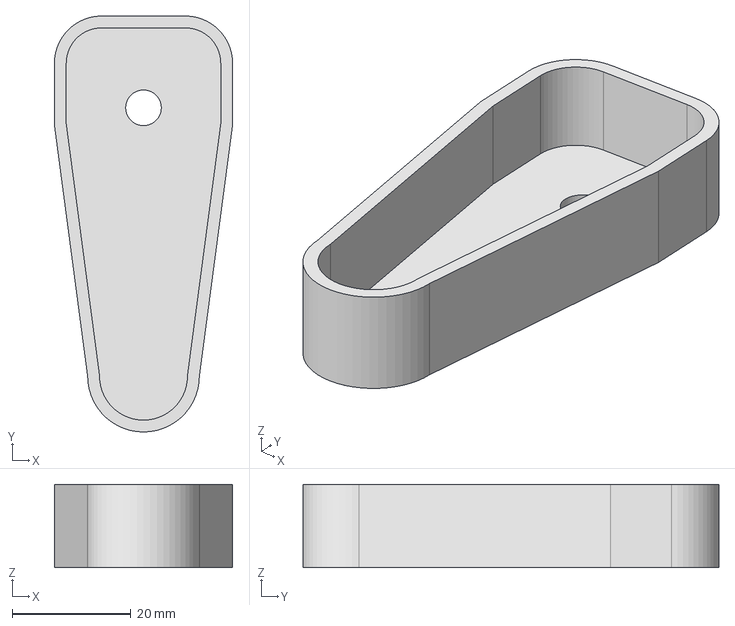
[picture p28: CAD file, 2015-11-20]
Zowi_3Dprintable/mods/Scopum/parts/step/arm_part1.step
30.0 x 70.0 x 14.0 mm

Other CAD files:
Zowi_3Dprintable/parts/step/footR.step
Zowi_3Dprintable/parts/step/chassis.step
Zowi_mold/plastic_parts/STP/Zowi_foot_cover.stp
Zowi_3Dprintable/mods/Scopum/parts/step/leg.step
Zowi_3Dprintable/mods/Scopum/parts/step/arm_part2.step
Zowi_3Dprintable/mods/Scopum/parts/step/arm_weapon_part1.step
Zowi_3Dprintable/mods/Scopum/parts/step/chassis.step
Zowi_3Dprintable/mods/Scopum/parts/step/footL.step
Zowi_3Dprintable/mods/Scopum/parts/step/footR.step
Zowi_3Dprintable/mods/Scopum/parts/stl/arm_part1.stl
Zowi_3Dprintable/mods/Scopum/parts/stl/arm_part2.stl
Zowi_3Dprintable/mods/Scopum/parts/stl/arm_weapon_part1.stl
Zowi_3Dprintable/mods/Scopum/parts/stl/arm_weapon_part2.stl
Zowi_3Dprintable/mods/Scopum/parts/stl/body.stl
Zowi_3Dprintable/mods/Scopum/parts/stl/chassis.stl
Zowi_3Dprintable/mods/Scopum/parts/stl/footL.stl
Zowi_3Dprintable/mods/Scopum/parts/stl/footR.stl
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

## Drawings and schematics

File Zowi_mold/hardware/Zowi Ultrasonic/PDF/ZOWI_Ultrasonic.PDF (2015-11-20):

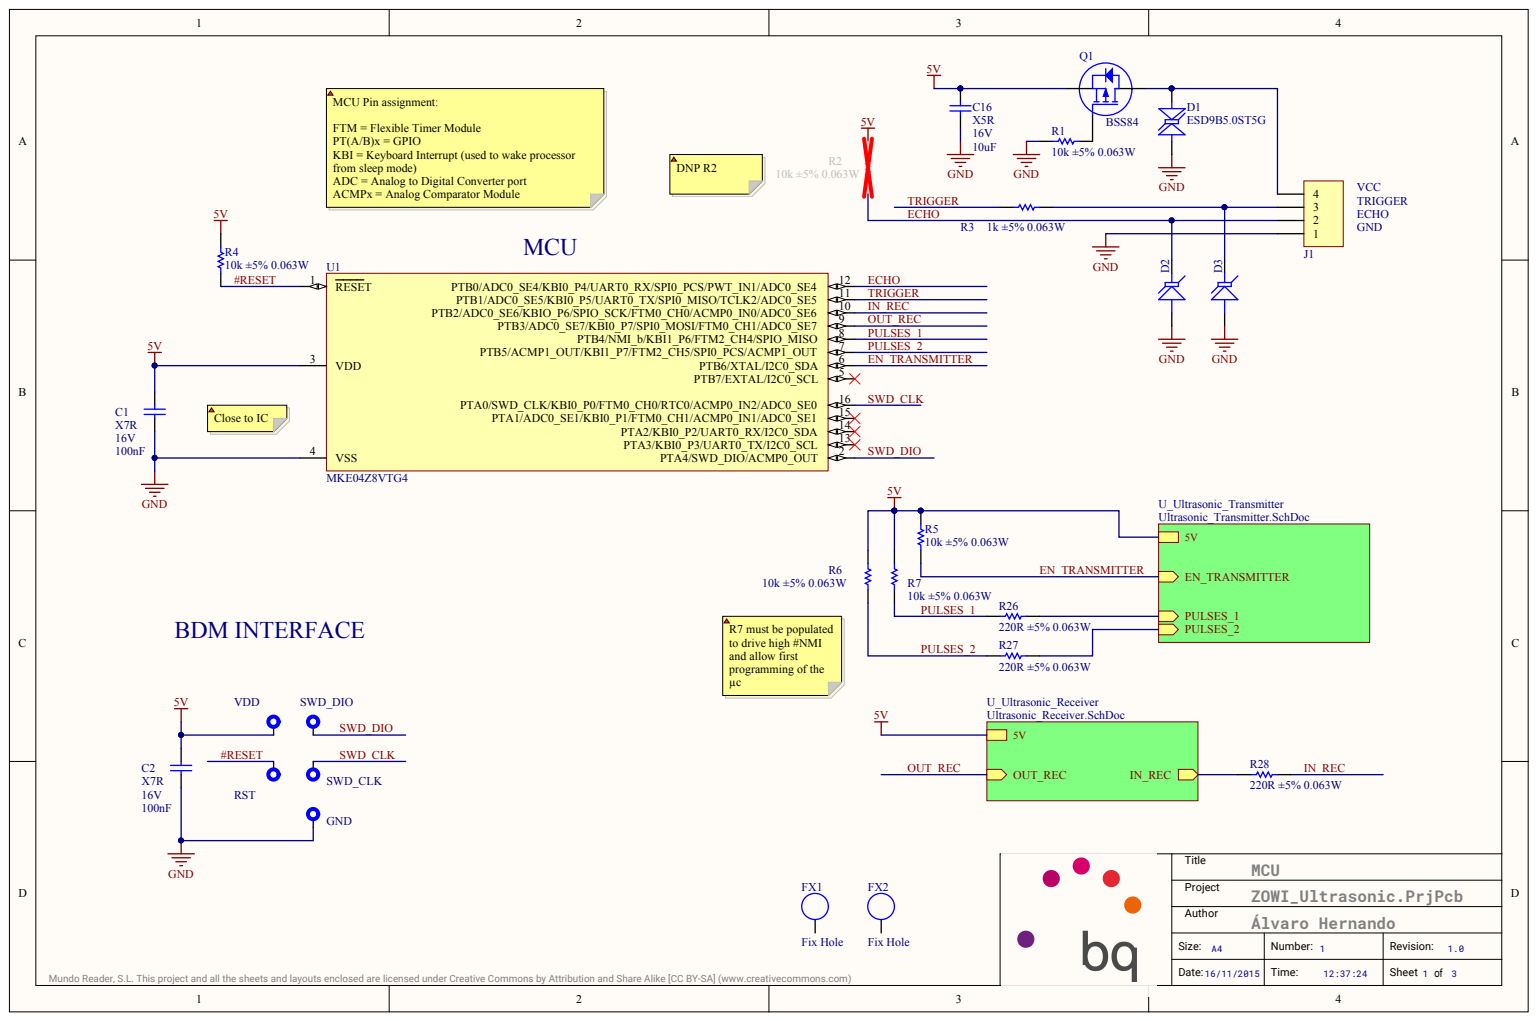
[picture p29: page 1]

FTM = Flexible Timer Module
PT(A/B)x = GPIO
KBI = Keyboard Interrupt (used to wake processor
from sleep mode)
ADC = Analog to Digital Converter port
ACMPx = Analog Comparator Module

R7 must be populated
to drive high #NMI
and allow first
programming of the µc

Size : A4 | Number: 1 | Revision: 1.0

Date : 16/11/2015 | Time : 12:37:24 | She e t of

Mundo Reader, S.L. This project and all the sheets and layouts enclosed are licensed under Creative Commons by Attribution and Share Alike [CC BY-SA] (www.creativecommons.com)

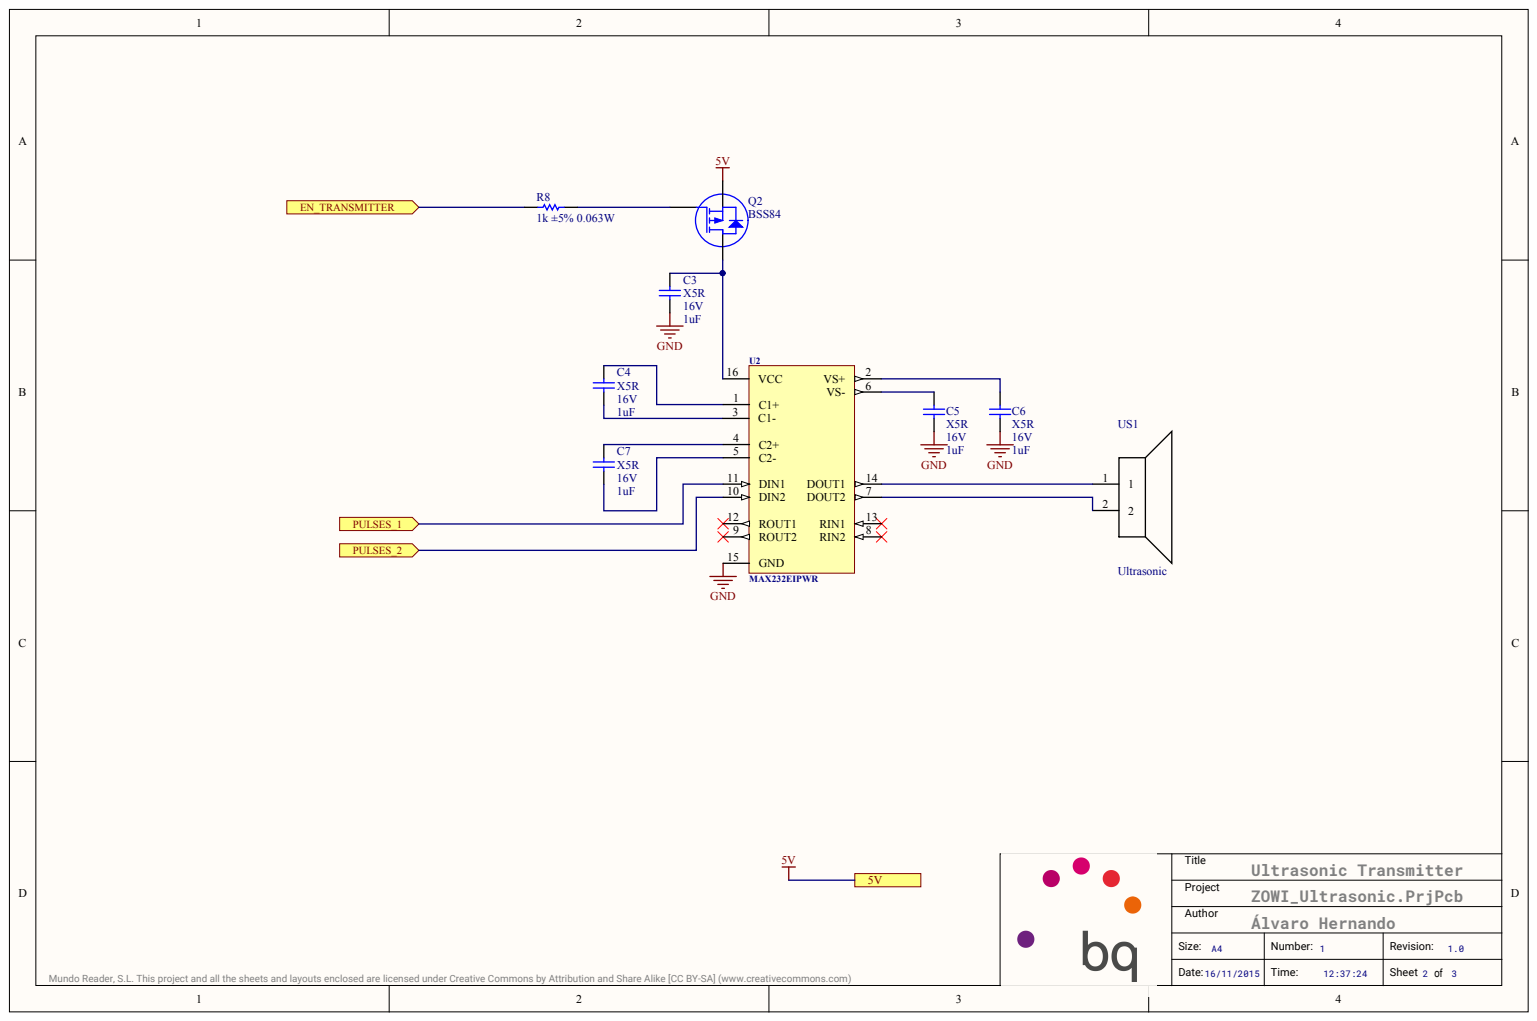
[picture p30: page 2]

X5R 16V | | DIN1 11

1uF | | DIN2 10

Size: A4 | Number: 1 | Revision: 1.0

Date: | Time: | Sheet 2 of 3

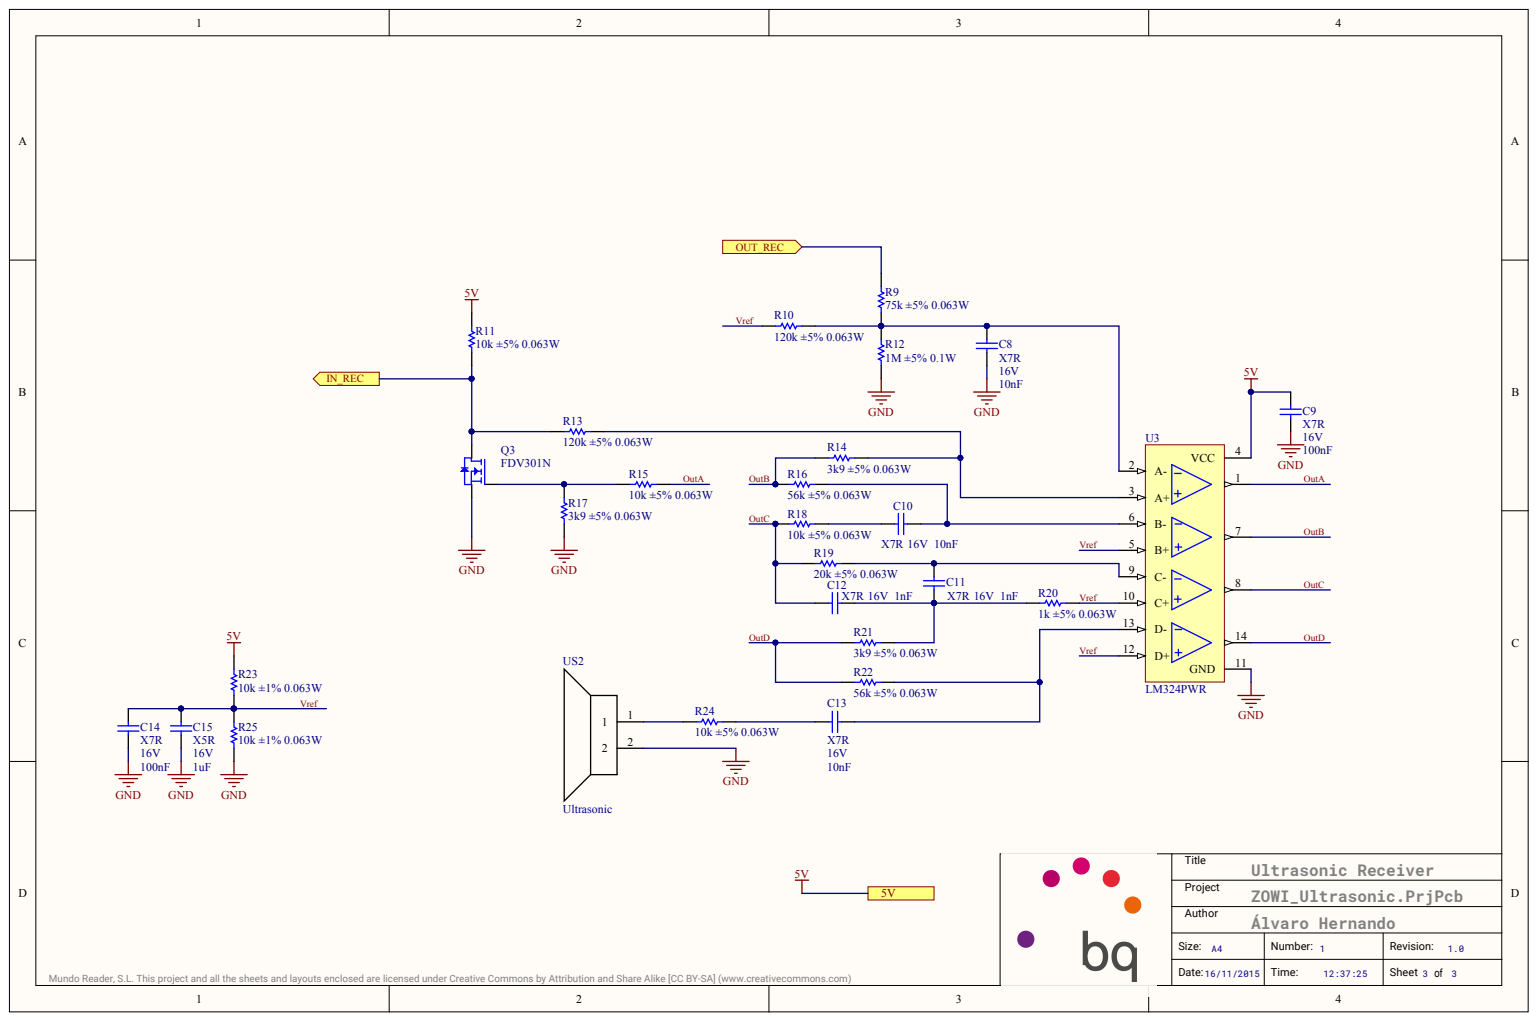
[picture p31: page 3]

R16 OutB | 3k9 ±5% 0.063W

Vref R22 | D+ 12

Size: A4 | Number: 1 | Revision: 1.0

Date: | Time: | Sheet 3 of 3

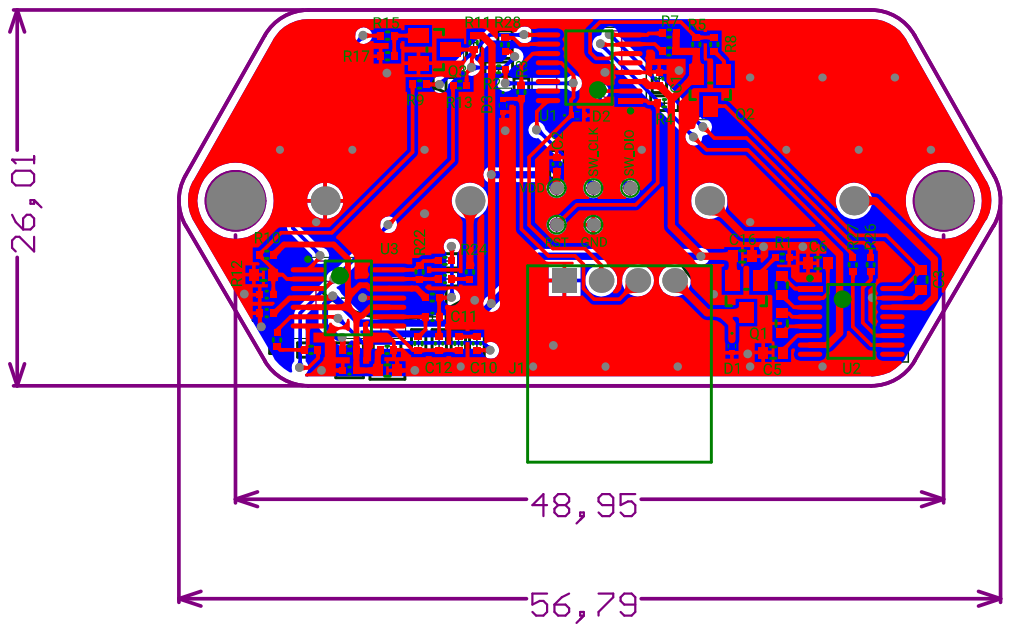
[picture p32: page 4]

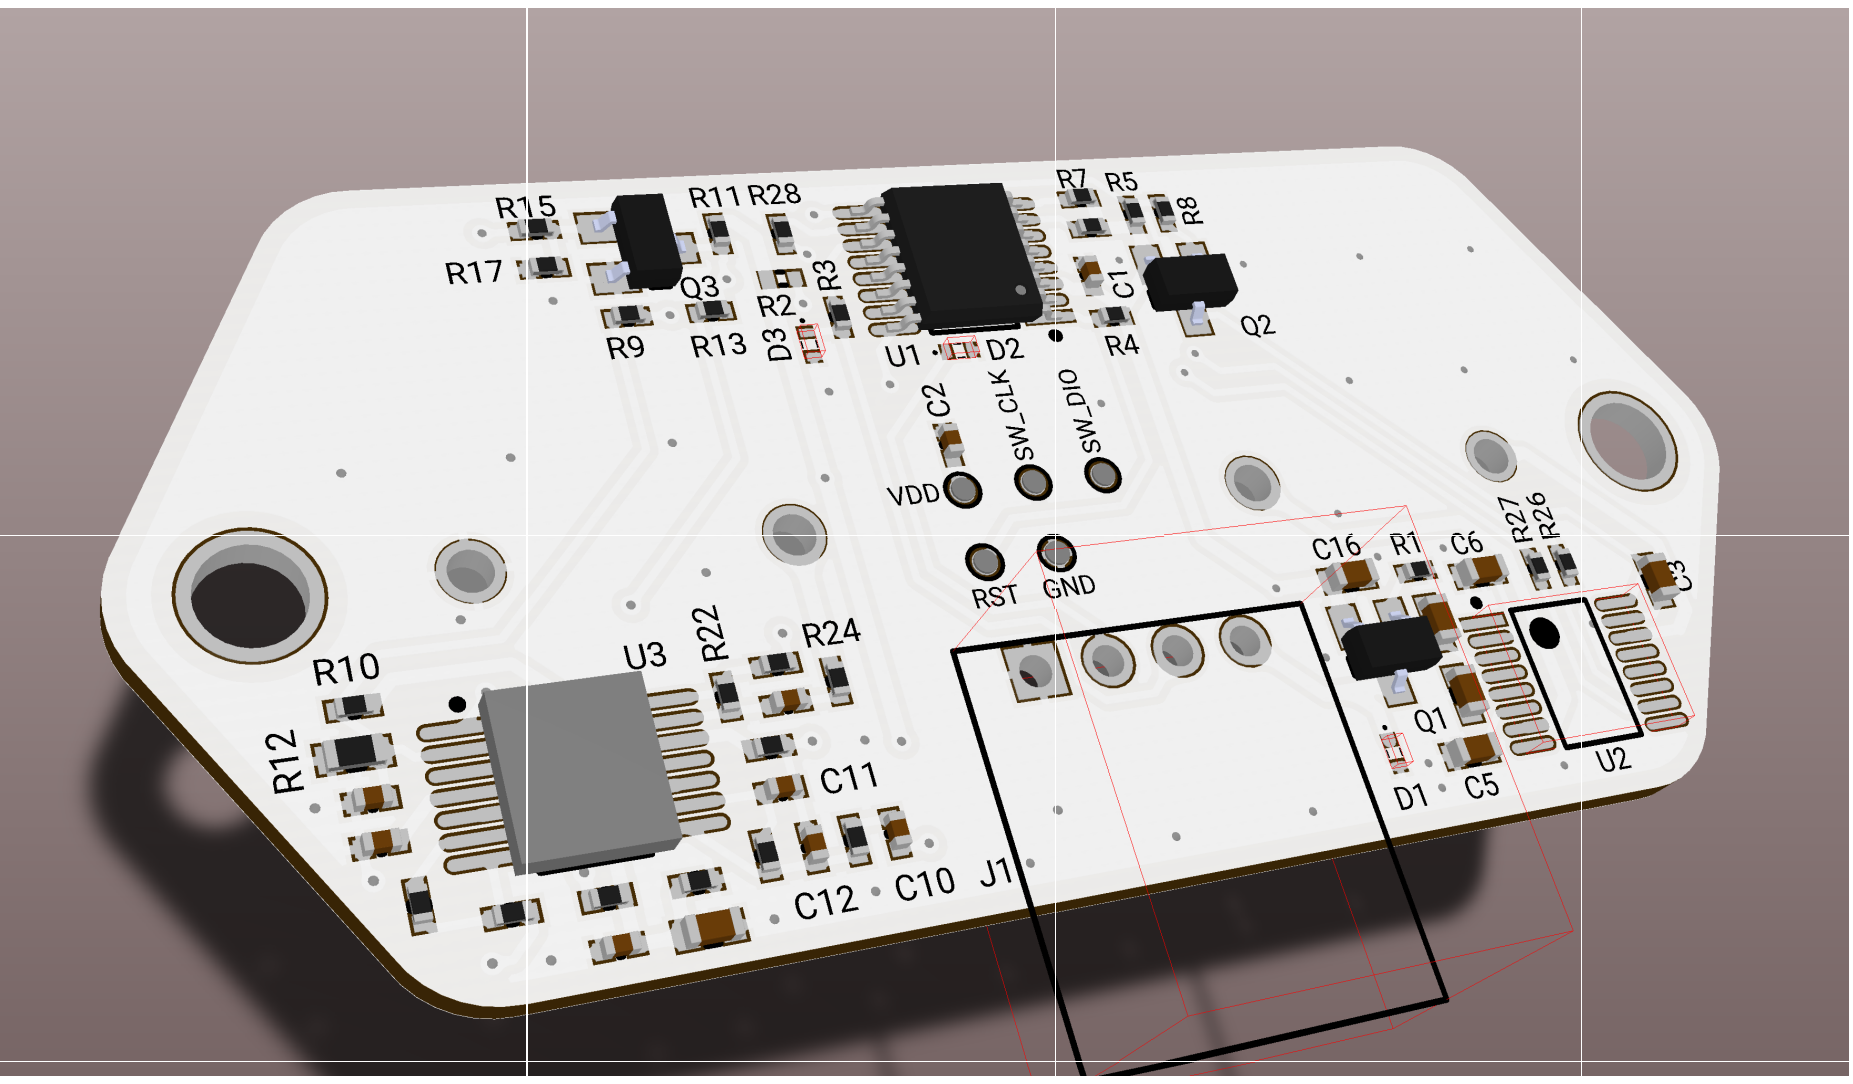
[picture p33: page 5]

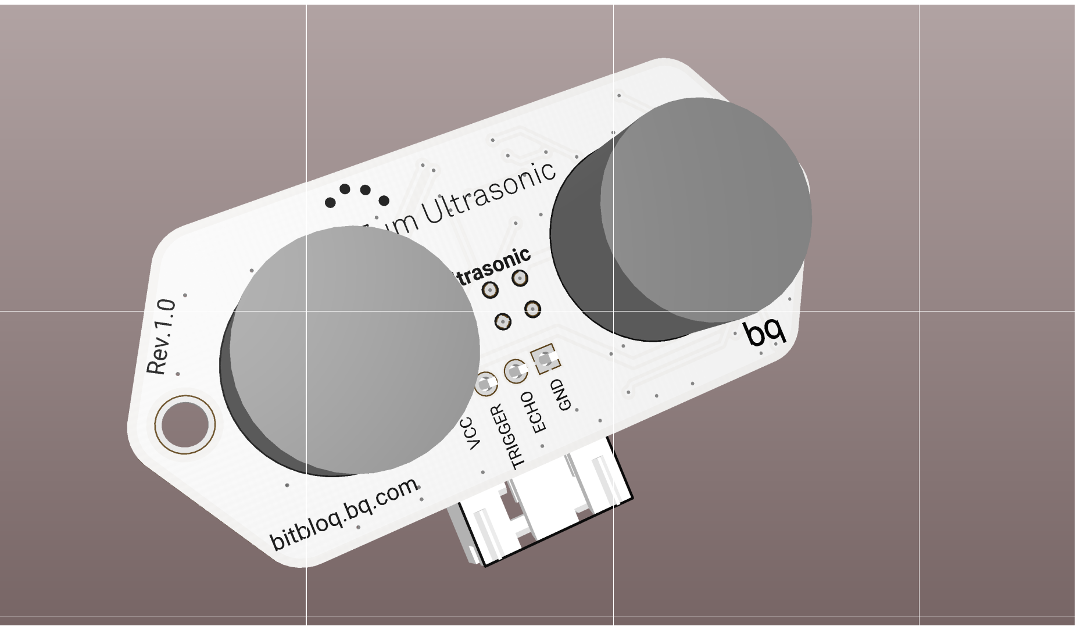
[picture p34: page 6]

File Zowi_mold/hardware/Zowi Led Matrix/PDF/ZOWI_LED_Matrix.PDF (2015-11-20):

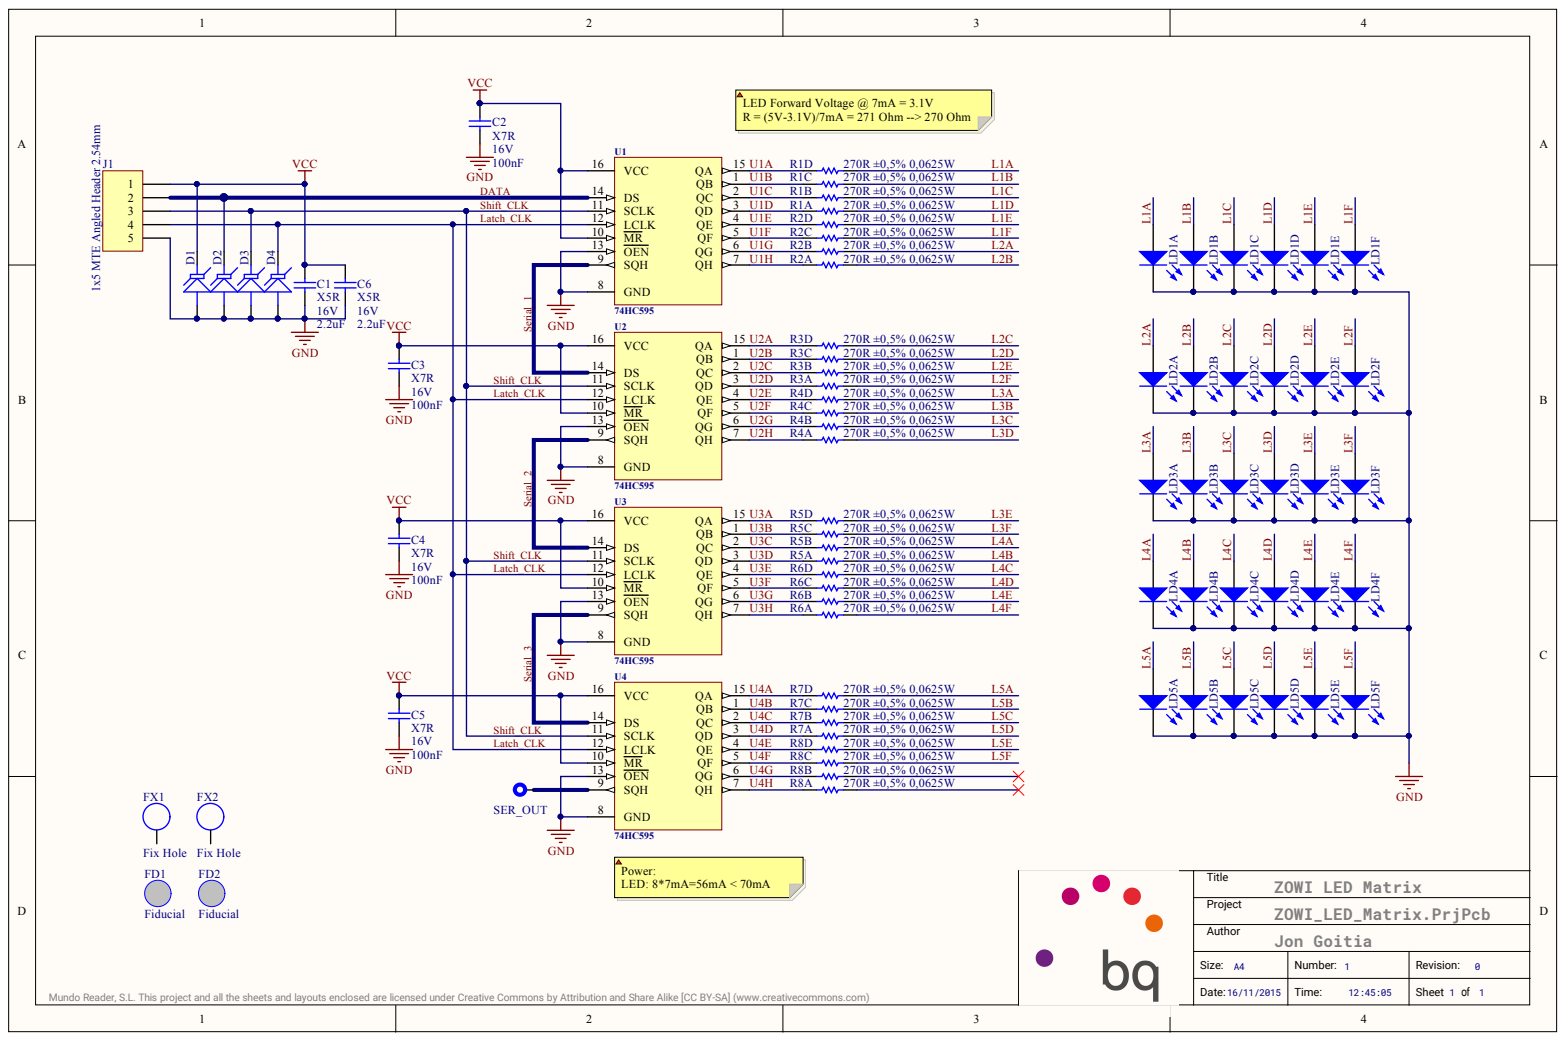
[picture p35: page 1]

Siz e : A 4 | Numbe r : 1 | R evision: 0

D ate : 1 6 / 1 1 / 2 0 1 5 | Time : 1 2 : 4 5 : 0 5 | She e t 1 o f 1

ive Commons by At

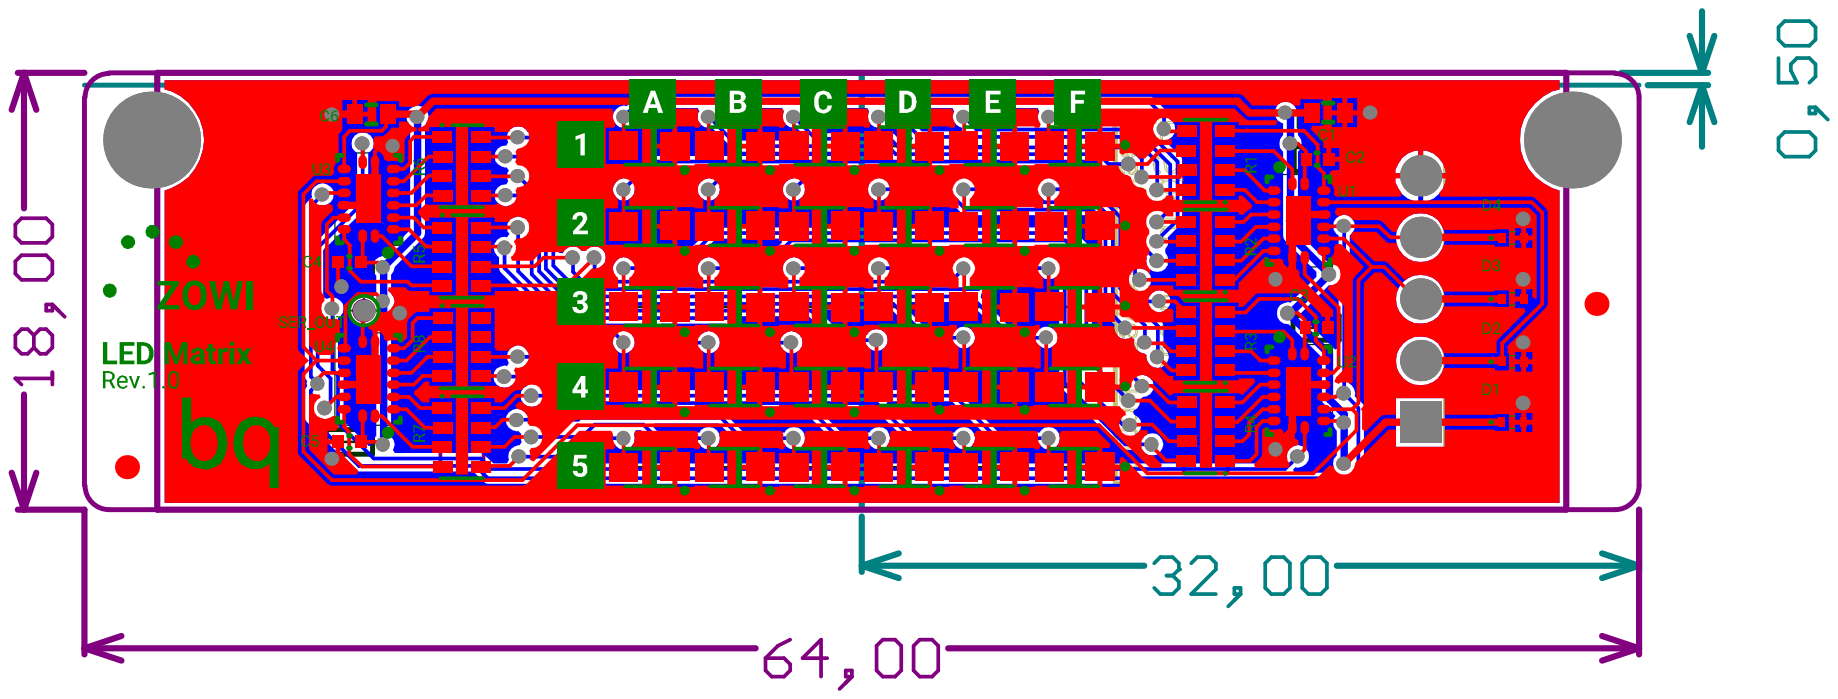
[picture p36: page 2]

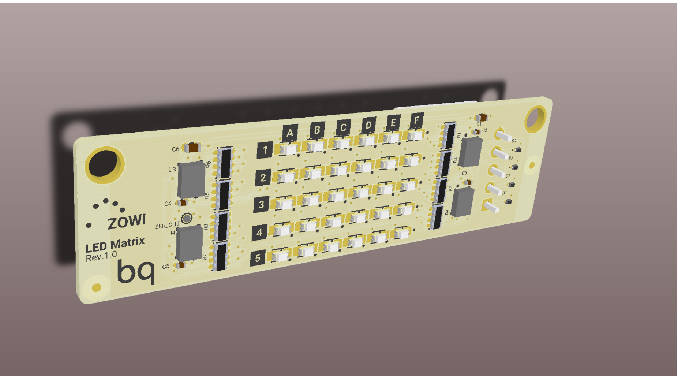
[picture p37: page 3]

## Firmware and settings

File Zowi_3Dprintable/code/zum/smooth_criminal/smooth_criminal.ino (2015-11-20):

#include <Servo.h>
#include <Oscillator.h>
#include <EEPROM.h>

#define N_SERVOS 4

//-- Have a look at the file zowi_walk_ino.ino for the documentation on how
//-- the servos are attached

#define EEPROM_TRIM 0 //Activar para coger los datos de calibracin desde la memoria interna

#define TRIM_RR -7
#define TRIM_RL -2
#define TRIM_YR  0
#define TRIM_YL -14

#define PIN_RR 5
#define PIN_RL 4
#define PIN_YR 3
#define PIN_YL 2

#define INTERVALTIME 10.0 

Oscillator servo[N_SERVOS];

void goingUp(int tempo);
void drunk (int tempo);
void noGravity(int tempo);
void kickLeft(int tempo);
void kickRight(int tempo);
void run(int steps, int T=500);
void walk(int steps, int T=1000);
void backyard(int steps, int T=3000);
void backyardSlow(int steps, int T=5000);
void turnLeft(int steps, int T=3000);
void turnRight(int steps, int T=3000);
void moonWalkLeft(int steps, int T=1000);
void moonWalkRight(int steps, int T=1000);
void crusaito(int steps, int T=1000);
void swing(int steps, int T=1000);
void upDown(int steps, int T=1000);
void flapping(int steps, int T=1000);

void setup()
{
  Serial.begin(19200);
  
  servo[0].attach(PIN_RR);
  servo[1].attach(PIN_RL);
  servo[2].attach(PIN_YR);
  servo[3].attach(PIN_YL);
  
  //EEPROM.write(0,TRIM_RR);
  //EEPROM.write(1,TRIM_RL);
  //EEPROM.write(2,TRIM_YR);
  //EEPROM.write(3,TRIM_YL);
  
  int trim;
  
  if(EEPROM_TRIM){
    for(int x=0;x<4;x++){
      trim=EEPROM.read(x);
      if(trim>128)trim=trim-256;
      Serial.print("TRIM ");
      Serial.print(x);
      Serial.print(" en ");
      Serial.println(trim);
      servo[x].SetTrim(trim);
    }
  }
  else{
    servo[0].SetTrim(TRIM_RR);
    servo[1].SetTrim(TRIM_RL);
    servo[2].SetTrim(TRIM_YR);
    servo[3].SetTrim(TRIM_YL);
  }
  
  for(int i=0;i<4;i++) servo[i].SetPosition(90);
}

// TEMPO: 121 BPM
int t=495;
double pause=0;

void loop()
{
 // if(Serial.available()){
  //  char init = Serial.read();
   // if (init=='X'){
   //   delay(4000); //3000 - 4500
   
dance();


//for(int i=0;i<4;i++) servo[i].SetPosition(90);

      
          for(int i=0;i<4;i++) servo[i].SetPosition(90);
   // }
 // }
}

void dance(){
  primera_parte();
  segunda_parte();
  moonWalkLeft(4,t*2);
  moonWalkRight(4,t*2);
  moonWalkLeft(4,t*2);
  moonWalkRight(4,t*2);
  primera_parte(); 
  crusaito(1,t*8);
  crusaito(1,t*7);

  for (int i=0; i<16; i++){
    flapping(1,t/4);
    delay(3*t/4);
  }
 
  moonWalkRight(4,t*2);
  moonWalkLeft(4,t*2);
  moonWalkRight(4,t*2);
  moonWalkLeft(4,t*2);

  drunk(t*4);
  drunk(t*4);
  drunk(t*4);
  drunk(t*4);
  kickLeft(t);
  kickRight(t);
  drunk(t*8);
  drunk(t*4);
  drunk(t/2);
  delay(t*4); 

  drunk(t/2);

  delay(t*4); 
  walk(2,t*2);
  backyard(2,t*2);
  goingUp(t*2);
  goingUp(t*1);
  noGravity(t*2);
  crusaito(1,t*2);
  crusaito(1,t*8);
  crusaito(1,t*2);
  crusaito(1,t*8);
  crusaito(1,t*2);
  crusaito(1,t*3);

  delay(t);
  primera_parte();
    for (int i=0; i<32; i++){
    flapping(1,t/2);
    delay(t/2);
  }
  
  for(int i=0;i<4;i++) servo[i].SetPosition(90);
}




////////////////////////////////////////////////////////////////////////////////////////
//////////////////////////////////FUNCIONES DE CONTROL//////////////////////////////////
////////////////////////////////////////////////////////////////////////////////////////

void oscillate(int A[N_SERVOS], int O[N_SERVOS], int T, double phase_diff[N_SERVOS]){
  for (int i=0; i<4; i++) {
    servo[i].SetO(O[i]);
    servo[i].SetA(A[i]);
    servo[i].SetT(T);
    servo[i].SetPh(phase_diff[i]);
  }
  double ref=millis();
   for (double x=ref; x<T+ref; x=millis()){
     for (int i=0; i<4; i++){
        servo[i].refresh();
     }
  }
}

unsigned long final_time;
unsigned long interval_time;
int oneTime;
int iteration;
float increment[N_SERVOS]; 
int oldPosition[]={90,90,90,90};

void moveNServos(int time, int  newPosition[]){
  for(int i=0;i<N_SERVOS;i++)	increment[i] = ((newPosition[i])-oldPosition[i])/(time/INTERVALTIME);
  
  final_time =  millis() + time; 
  
  iteration = 1; 
  while(millis() < final_time){ //Javi del futuro cambia esto  
      interval_time = millis()+INTERVALTIME;  
      
      oneTime=0;      
      while(millis()<interval_time){	  
          if(oneTime<1){ 
              for(int i=0;i<N_SERVOS;i++){
                  servo[i].SetPosition(oldPosition[i] + (iteration * increment[i]));
              }			
              iteration++;
              oneTime++;
          }
      }     
  }   

  for(int i=0;i<N_SERVOS;i++){	
    oldPosition[i] = newPosition[i];
  }   
}


//////////////////////////////////////////////////////////////////////////////
////////////////////////////////PASOS DE BAILE////////////////////////////////
//////////////////////////////////////////////////////////////////////////////

void goingUp(int tempo){
  
      pause=millis();
      for(int i=0;i<4;i++) servo[i].SetPosition(90);
      delay(tempo);
      servo[0].SetPosition(80);
      servo[1].SetPosition(100);
      delay(tempo);
      servo[0].SetPosition(70);
      servo[1].SetPosition(110);
      delay(tempo);
      servo[0].SetPosition(60);
      servo[1].SetPosition(120);
      delay(tempo);
      servo[0].SetPosition(50);
      servo[1].SetPosition(130);
      delay(tempo);
      servo[0].SetPosition(40);
      servo[1].SetPosition(140);
      delay(tempo);
      servo[0].SetPosition(30);
      servo[1].SetPosition(150);
      delay(tempo);
      servo[0].SetPosition(20);
      servo[1].SetPosition(160);
      delay(tempo);
      
      while(millis()<pause+8*t);

}

void primera_parte(){
  
  int move1[4] = {60,120,90,90};
  int move2[4] = {90,90,90,90};
  int move3[4] = {40,140,90,90};
  
  for(int x=0; x<3; x++){
    for(int i=0; i<3; i++){
      lateral_fuerte(1,t/2);
      lateral_fuerte(0,t/4);
      lateral_fuerte(1,t/4);
      delay(t);
    }
  
    pause=millis();
    for(int i=0;i<4;i++) servo[i].SetPosition(90);
    moveNServos(t*0.4,move1);
    moveNServos(t*0.4,move2);
    while(millis()<(pause+t*2));
  }
  
  for(int i=0; i<2; i++){
    lateral_fuerte(1,t/2);
    lateral_fuerte(0,t/4);
    lateral_fuerte(1,t/4);
    delay(t);
  }
    
  pause=millis();
  for(int i=0;i<4;i++) servo[i].SetPosition(90);
  crusaito(1,t*1.4);
  moveNServos(t*1,move3);
  for(int i=0;i<4;i++) servo[i].SetPosition(90);
  while(millis()<(pause+t*4));
}

void segunda_parte(){
  
  int move1[4] = {90,90,80,100};
  int move2[4] = {90,90,100,80};
  int move3[4] = {90,90,80,100};
  int move4[4] = {90,90,100,80};
    
  int move5[4] = {40,140,80,100};
  int move6[4] = {40,140,100,80};
  int move7[4] = {90,90,80,100};
  int move8[4] = {90,90,100,80};
       
  int move9[4] = {40,140,80,100};
  int move10[4] = {40,140,100,80};
  int move11[4] = {90,90,80,100};
  int move12[4] = {90,90,100,80};
  
  for(int x=0; x<7; x++){ 
    for(int i=0; i<3; i++){
      pause=millis();
      moveNServos(t*0.15,move1);
      moveNServos(t*0.15,move2);
      moveNServos(t*0.15,move3);
      moveNServos(t*0.15,move4);
      while(millis()<(pause+t));
    }
    pause=millis();
    moveNServos(t*0.15,move5);
    moveNServos(t*0.15,move6);
    moveNServos(t*0.15,move7);
    moveNServos(t*0.15,move8);
    while(millis()<(pause+t));
  }
 
  for(int i=0; i<3; i++){
    pause=millis();
    moveNServos(t*0.15,move9);
    moveNServos(t*0.15,move10);
    moveNServos(t*0.15,move11);
    moveNServos(t*0.15,move12);
    while(millis()<(pause+t));
  }
}

void lateral_fuerte(boolean side, int tempo){
  
  for(int i=0;i<4;i++) servo[i].SetPosition(90);
  if (side) servo[0].SetPosition(40);
  else servo[1].SetPosition(140);
  delay(tempo/2);
  servo[0].SetPosition(90);
  servo[1].SetPosition(90);
  delay(tempo/2);

}

void drunk (int tempo){
  
  pause=millis();
  
  int move1[] = {60,70,90,90};
  int move2[] = {110,120,90,90};
  int move3[] = {60,70,90,90};
  int move4[] = {110,120,90,90};
  
  moveNServos(tempo*0.235,move1);
  moveNServos(tempo*0.235,move2);
  moveNServos(tempo*0.235,move3);
  moveNServos(tempo*0.235,move4);
  while(millis()<(pause+tempo));

}


void noGravity(int tempo){
  
  int move1[4] = {120,140,90,90};
  int move2[4] = {140,140,90,90};
  int move3[4] = {120,140,90,90};
  int move4[4] = {90,90,90,90};
  
  
  for(int i=0;i<4;i++) servo[i].SetPosition(90);
  for(int i=0;i<N_SERVOS;i++) oldPosition[i]=90;
  moveNServos(tempo*2,move1);
  moveNServos(tempo*2,move2);
  delay(tempo*2);
  moveNServos(tempo*2,move3);
  moveNServos(tempo*2,move4);

 

}

void kickLeft(int tempo){
  for(int i=0;i<4;i++) servo[i].SetPosition(90);
  delay(tempo);
  servo[0].SetPosition(50); //pie derecho
  servo[1].SetPosition(70); //pie izquiero
  delay(tempo);
  servo[0].SetPosition(80); //pie derecho
  servo[1].SetPosition(70); //pie izquiero
  delay(tempo/4);
  servo[0].SetPosition(30); //pie derecho
  servo[1].SetPosition(70); //pie izquiero
  delay(tempo/4);
  servo[0].SetPosition(80); //pie derecho
  servo[1].SetPosition(70); //pie izquiero
  delay(tempo/4);
  servo[0].SetPosition(30); //pie derecho
  servo[1].SetPosition(70); //pie izquiero
  delay(tempo/4);
  servo[0].SetPosition(80); //pie derecho
  servo[1].SetPosition(70); //pie izquiero
  delay(tempo);
}

void kickRight(int tempo){
for(int i=0;i<4;i++) servo[i].SetPosition(90);
  delay(tempo);
  servo[0].SetPosition(110); //pie derecho
  servo[1].SetPosition(130); //pie izquiero
  delay(tempo);
  servo[0].SetPosition(110); //pie derecho
  servo[1].SetPosition(100); //pie izquiero
  delay(tempo/4);
  servo[0].SetPosition(110); //pie derecho
  servo[1].SetPosition(150); //pie izquiero
  delay(tempo/4);
  servo[0].SetPosition(110); //pie derecho
  servo[1].SetPosition(80); //pie izquiero
  delay(tempo/4);
  servo[0].SetPosition(110); //pie derecho
  servo[1].SetPosition(150); //pie izquiero
  delay(tempo/4);
  servo[0].SetPosition(110); //pie derecho
  servo[1].SetPosition(100); //pie izquiero
  delay(tempo);
}

void walk(int steps, int T){
    int A[4]= {15, 15, 30, 30};
    int O[4] = {0, 0, 0, 0};
    double phase_diff[4] = {DEG2RAD(0), DEG2RAD(0), DEG2RAD(90), DEG2RAD(90)};
    
    for(int i=0;i<steps;i++)oscillate(A,O, T, phase_diff);
}

void run(int steps, int T){
    int A[4]= {10, 10, 10, 10};
    int O[4] = {0, 0, 0, 0};
    double phase_diff[4] = {DEG2RAD(0), DEG2RAD(0), DEG2RAD(90), DEG2RAD(90)}; 
    
    for(int i=0;i<steps;i++)oscillate(A,O, T, phase_diff);
}

void backyard(int steps, int T){
    int A[4]= {15, 15, 30, 30};
    int O[4] = {0, 0, 0, 0};
    double phase_diff[4] = {DEG2RAD(0), DEG2RAD(0), DEG2RAD(-90), DEG2RAD(-90)}; 
    
    for(int i=0;i<steps;i++)oscillate(A,O, T, phase_diff);
}

void backyardSlow(int steps, int T){
    int A[4]= {15, 15, 30, 30};
    int O[4] = {0, 0, 0, 0};
    double phase_diff[4] = {DEG2RAD(0), DEG2RAD(0), DEG2RAD(-90), DEG2RAD(-90)}; 
    
    for(int i=0;i<steps;i++)oscillate(A,O, T, phase_diff);
}


void turnLeft(int steps, int T){
    int A[4]= {20, 20, 10, 30};
    int O[4] = {0, 0, 0, 0};
    double phase_diff[4] = {DEG2RAD(0), DEG2RAD(0), DEG2RAD(90), DEG2RAD(90)}; 
    
    for(int i=0;i<steps;i++)oscillate(A,O, T, phase_diff);
}

void turnRight(int steps, int T){
    int A[4]= {20, 20, 30, 10};
    int O[4] = {0, 0, 0, 0};
    double phase_diff[4] = {DEG2RAD(0), DEG2RAD(0), DEG2RAD(90), DEG2RAD(90)}; 
    
    for(int i=0;i<steps;i++)oscillate(A,O, T, phase_diff);
}

void moonWalkRight(int steps, int T){
    int A[4]= {25, 25, 0, 0};
    int O[4] = {-15 ,15, 0, 0};
    double phase_diff[4] = {DEG2RAD(0), DEG2RAD(180 + 120), DEG2RAD(90), DEG2RAD(90)}; 
    
    for(int i=0;i<steps;i++)oscillate(A,O, T, phase_diff);
}

void moonWalkLeft(int steps, int T){
    int A[4]= {25, 25, 0, 0};
    int O[4] = {-15, 15, 0, 0};
    double phase_diff[4] = {DEG2RAD(0), DEG2RAD(180 - 120), DEG2RAD(90), DEG2RAD(90)}; 
    
    for(int i=0;i<steps;i++)oscillate(A,O, T, phase_diff);
}

void crusaito(int steps, int T){
    int A[4]= {25, 25, 30, 30};
    int O[4] = {- 15, 15, 0, 0};
    double phase_diff[4] = {DEG2RAD(0), DEG2RAD(180 + 120), DEG2RAD(90), DEG2RAD(90)}; 
    
    for(int i=0;i<steps;i++)oscillate(A,O, T, phase_diff);
}

void swing(int steps, int T){
    int A[4]= {25, 25, 0, 0};
    int O[4] = {-15, 15, 0, 0};
    double phase_diff[4] = {DEG2RAD(0), DEG2RAD(0), DEG2RAD(90), DEG2RAD(90)};
    
    for(int i=0;i<steps;i++)oscillate(A,O, T, phase_diff);
}

void upDown(int steps, int T){
    int A[4]= {25, 25, 0, 0};
    int O[4] = {-15, 15, 0, 0};
    double phase_diff[4] = {DEG2RAD(180), DEG2RAD(0), DEG2RAD(270), DEG2RAD(270)};
    
    for(int i=0;i<steps;i++)oscillate(A,O, T, phase_diff);
}

void flapping(int steps, int T){
    int A[4]= {15, 15, 8, 8};
    int O[4] = {-A[0], A[1], 0, 0};
    double phase_diff[4] = {DEG2RAD(0), DEG2RAD(180), DEG2RAD(90), DEG2RAD(-90)};
    
    for(int i=0;i<steps;i++)oscillate(A,O, T, phase_diff);
}

void test(int steps, int T){
    int A[4]= {15, 15, 8, 8};
    int O[4] = {-A[0] + 10, A[1] - 10, 0, 0};
    double phase_diff[4] = {DEG2RAD(0), DEG2RAD(180), DEG2RAD(90), DEG2RAD(-90)};
    
    for(int i=0;i<steps;i++)oscillate(A,O, T, phase_diff);
}
